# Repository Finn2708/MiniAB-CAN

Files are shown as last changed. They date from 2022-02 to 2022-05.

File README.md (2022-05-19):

# MiniAB-CAN
Toolhead board with CAN interface for [Voron Mini Afterburner](https://github.com/VoronDesign/Voron-0) and [Voron Stealthburner](https://github.com/VoronDesign/Voron-Afterburner/tree/sb-beta).

Features:
- CAN bus interface
- TMC2209 stepper driver for extruder motor
- Integrated ADXL345 for resonance compensation
- Neopixel Output for toolhead LEDs
- Two endstop and one probe port
- User-selectable fan voltages (5V/24V)

---

## Table of Contents
- [Prototype](#prototype)
  - [Size comparison](#size)
  - [Thermal images](#thermal-images)
- [Pinout](#pinout)
- [Interactive BOM](https://finn2708.github.io/MiniAB-CAN/index.html)

## Prototype
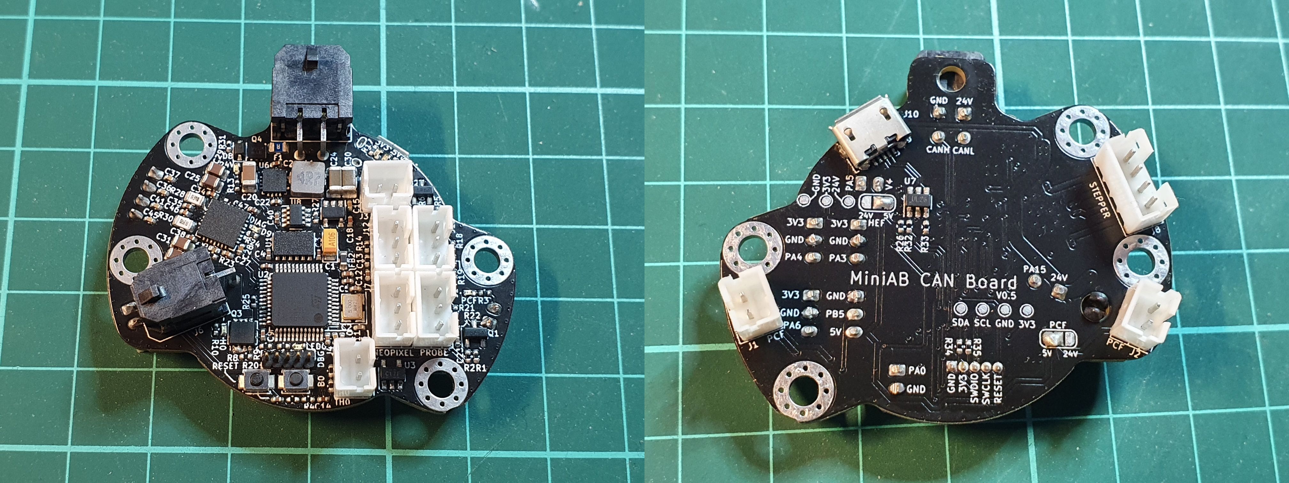
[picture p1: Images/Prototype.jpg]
Prototype


### Size
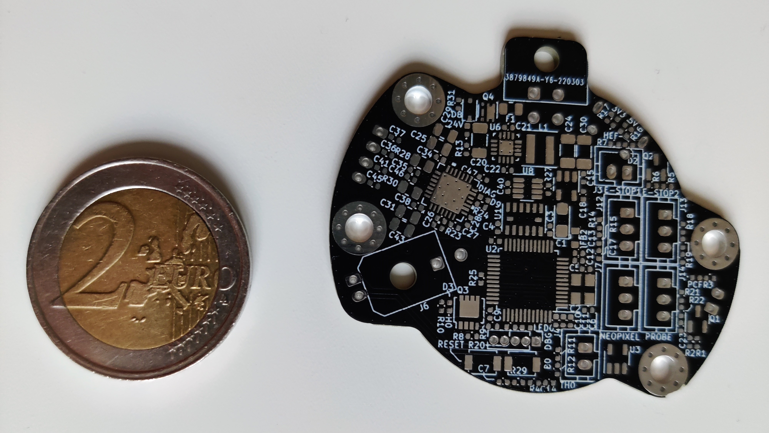
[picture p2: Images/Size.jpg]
Size


### Thermal images
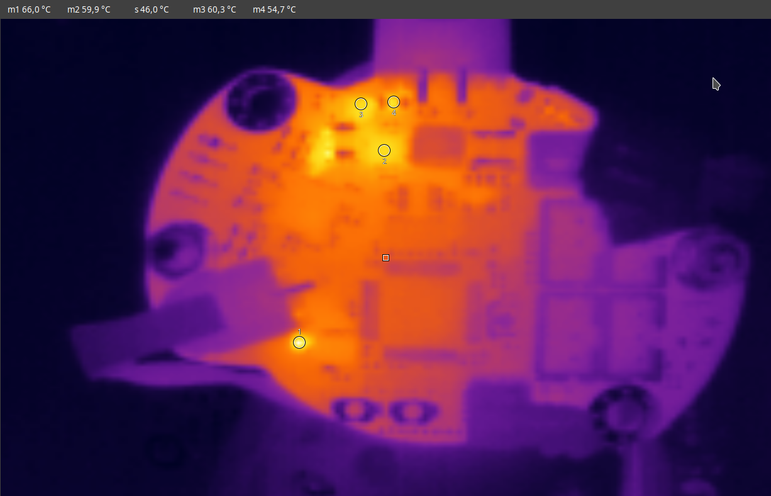
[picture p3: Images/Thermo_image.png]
Thermal images


## Pinout
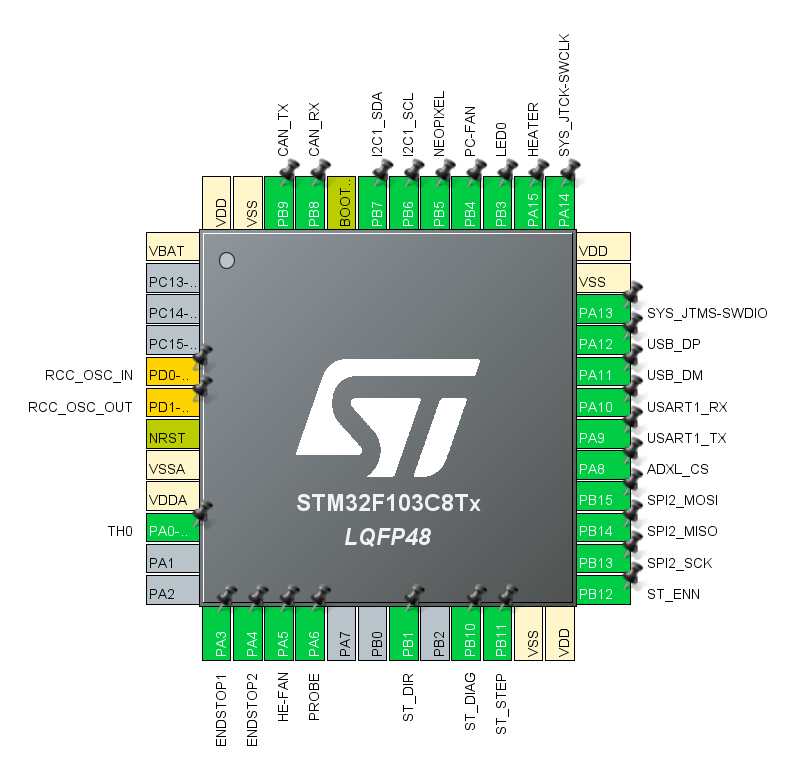
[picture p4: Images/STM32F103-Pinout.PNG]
Pinout

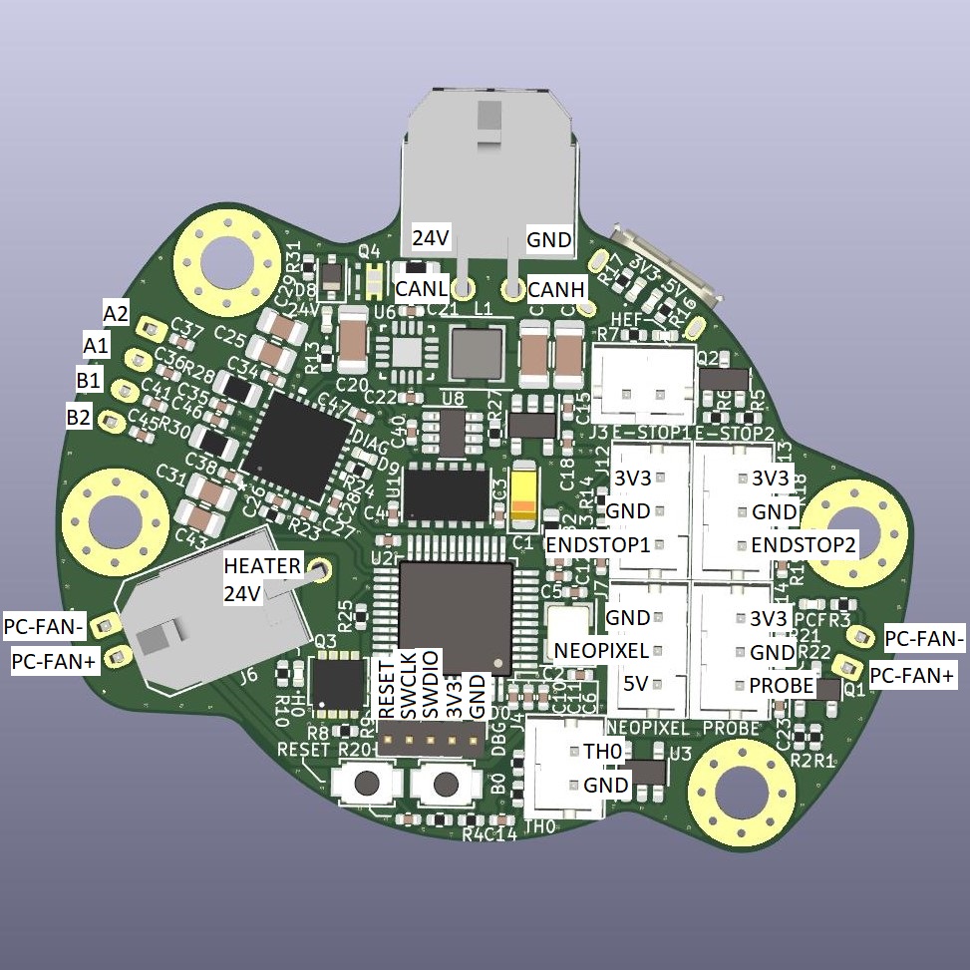
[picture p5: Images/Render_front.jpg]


## BOM
[Interactive BOM](https://finn2708.github.io/MiniAB-CAN/index.html)

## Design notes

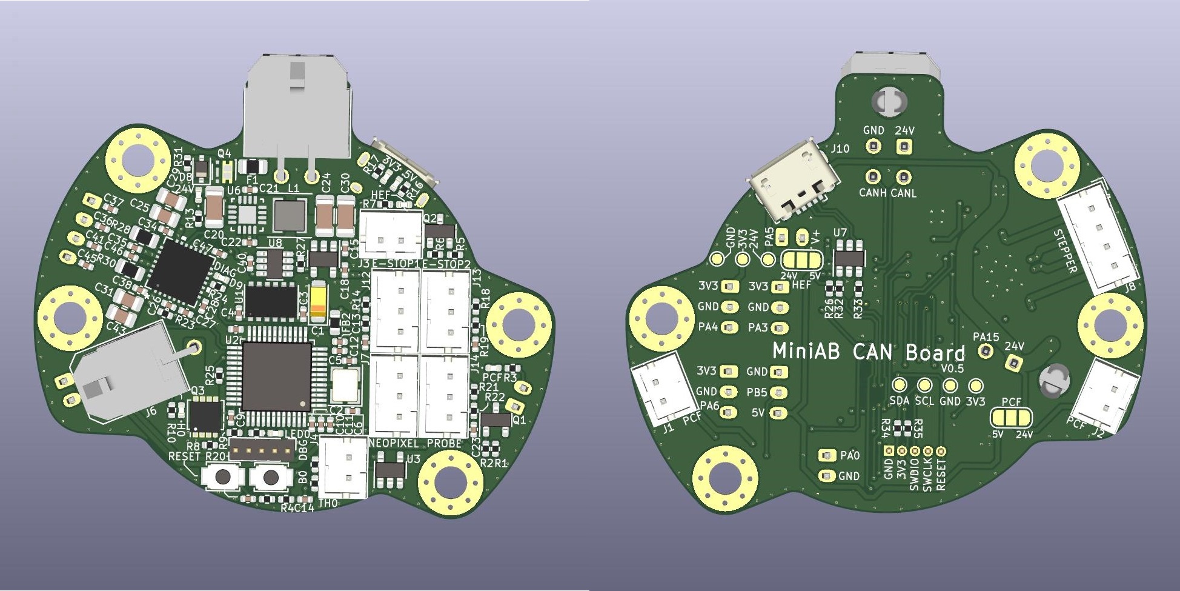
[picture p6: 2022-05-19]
Images/Render.jpg

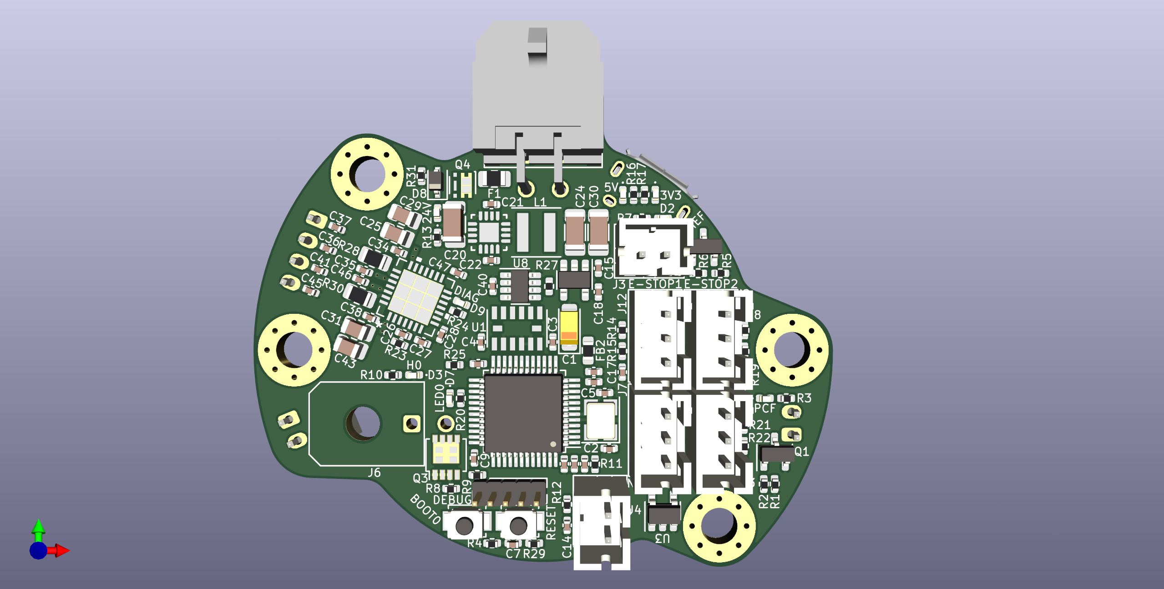
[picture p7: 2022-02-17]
PCB/MiniAB-CAN-Board_top.png

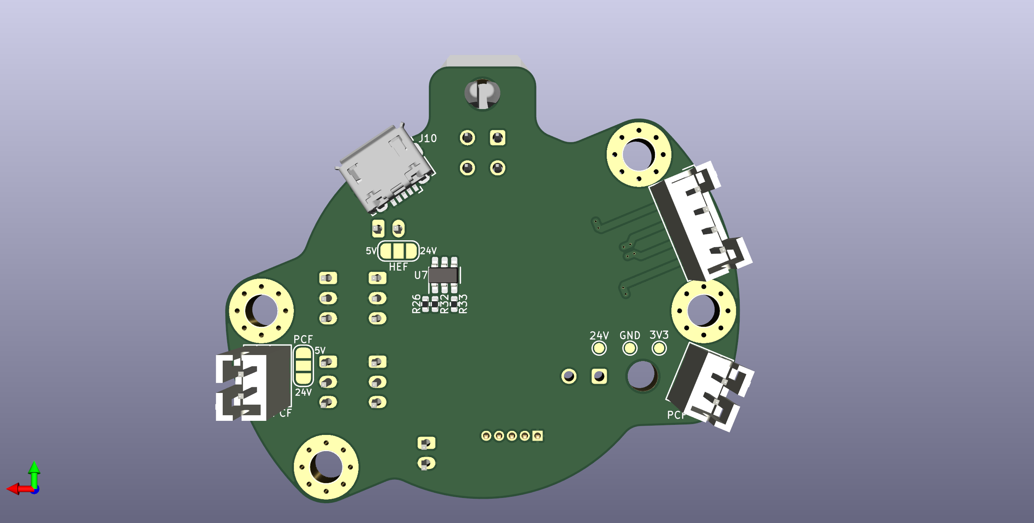
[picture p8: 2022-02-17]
PCB/MiniAB-CAN-Board_bottom.png

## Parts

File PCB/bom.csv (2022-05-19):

Comment | Designator | Footprint | LCSC
10u | C1 | Capacitor_Tantalum_SMD:CP_EIA-3216-18_Kemet-A
12p | C2,C5 | Capacitor_SMD:C_0402_1005Metric
100n | C3,C4,C6,C7,C8,C9,C10,C12,C14,C17,C19,C23,C40,C47 | Capacitor_SMD:C_0402_1005Metric
4.7u | C11,C28 | Capacitor_SMD:C_0402_1005Metric
1u | C13,C18 | Capacitor_SMD:C_0402_1005Metric
2u2 | C15 | Capacitor_SMD:C_0402_1005Metric
10u/35V | C20 | Capacitor_SMD:C_1206_3216Metric
100n/35V | C21,C27,C34,C35,C38,C46 | Capacitor_SMD:C_0402_1005Metric
22n | C22 | Capacitor_SMD:C_0402_1005Metric
22u | C24,C30 | Capacitor_SMD:C_1206_3216Metric
10u/35V | C25,C29,C31,C43 | Capacitor_SMD:C_0805_2012Metric
22n/50V | C26 | Capacitor_SMD:C_0402_1005Metric
1n/50V | C36,C37,C41,C45 | Capacitor_SMD:C_0402_1005Metric
RED | D1,D2,D3,D4,D5,D6,D7,D9 | LED_SMD:LED_0402_1005Metric
15V | D8 | Diode_SMD:D_SOD-323
3.5A | F1 | Fuse:Fuse_0805_2012Metric
GZ1608D601TF | FB2 | Resistor_SMD:R_0603_1608Metric
PCF | J1,J2 | Connector_JST:JST_PH_B2B-PH-K_1x02_P2.00mm_Vertical
HEF | J3 | Connector_JST:JST_PH_B2B-PH-K_1x02_P2.00mm_Vertical
TH0 | J4 | Connector_JST:JST_PH_B2B-PH-K_1x02_P2.00mm_Vertical
H0 | J6 | Connector_Molex:Molex_Micro-Fit_3.0_43045-0200_2x01_P3.00mm_Horizontal
NEOPIXEL | J7 | Connector_JST:JST_PH_B3B-PH-K_1x03_P2.00mm_Vertical
STEPPER | J8 | Connector_JST:JST_PH_B4B-PH-K_1x04_P2.00mm_Vertical
DEBUG | J9 | Connector_PinHeader_1.27mm:PinHeader_1x05_P1.27mm_Vertical
USB_B_Micro | J10 | Connector_USB:USB_Micro-B_Amphenol_10118194_Horizontal
CAN | J11 | Connector_Molex:Molex_Micro-Fit_3.0_43045-0400_2x02_P3.00mm_Horizontal
E-STOP1 | J12 | Connector_JST:JST_PH_B3B-PH-K_1x03_P2.00mm_Vertical
E-STOP2 | J13 | Connector_JST:JST_PH_B3B-PH-K_1x03_P2.00mm_Vertical
PROBE | J14 | Connector_JST:JST_PH_B3B-PH-K_1x03_P2.00mm_Vertical
4.7u | L1 | Inductor_SMD:L_Coilcraft_XxL4020
AO3400A | Q1,Q2 | Package_TO_SOT_SMD:SOT-23
AON7418 | Q3 | footprints:AON7418
SiA449DJ | Q4 | Package_TO_SOT_SMD:Vishay_PowerPAK_SC70-6L_Single
10k | R1,R4,R5,R8,R12,R14,R15,R18,R19,R21,R22 | Resistor_SMD:R_0402_1005Metric
150 | R2,R6,R9 | Resistor_SMD:R_0402_1005Metric
2.2k | R3,R7,R10,R13 | Resistor_SMD:R_0402_1005Metric
2.2k 0.1% | R11 | Resistor_SMD:R_0402_1005Metric
300 | R16 | Resistor_SMD:R_0402_1005Metric
120 | R17,R20,R24 | Resistor_SMD:R_0402_1005Metric
100k | R23,R29,R31 | Resistor_SMD:R_0402_1005Metric
1k | R25 | Resistor_SMD:R_0402_1005Metric
1.5k | R26 | Resistor_SMD:R_0402_1005Metric
120R | R27 | Resistor_SMD:R_0402_1005Metric
0.5Ω, 1%, 0.5W, 1210 | R28,R30 | Resistor_SMD:R_0805_2012Metric
27 | R32,R33 | Resistor_SMD:R_0402_1005Metric
4.7k | R34,R35 | Resistor_SMD:R_0402_1005Metric
RESET | SW1 | Button_Switch_SMD:SW_SPST_B3U-1000P
BOOT0 | SW2 | Button_Switch_SMD:SW_SPST_B3U-1000P
ADXL345BCCZ-RL7 | U1 | footprints:ADXL345BCCZ-RL7
STM32F103C8Tx | U2 | Package_QFP:LQFP-48_7x7mm_P0.5mm
74LVC1G17 | U3 | Package_TO_SOT_SMD:SOT-23-5
LP5907MFX-3.3 | U4 | Package_TO_SOT_SMD:SOT-23-5
TMC2209-LA | U5 | footprints:TMC2209-LA
TS30041-M050QFNR | U6 | TS30041:Semtech-QFN16-0-0-0
USBLC6-2SC6 | U7 | Package_TO_SOT_SMD:SOT-23-6
TCAN330 | U8 | Package_TO_SOT_SMD:TSOT-23-8
8MHz | Y1 | Crystal:Crystal_SMD_3225-4Pin_3.2x2.5mm

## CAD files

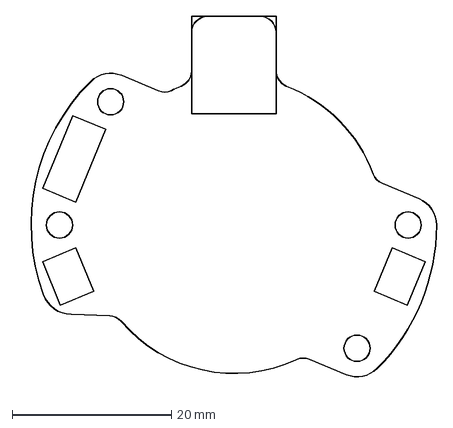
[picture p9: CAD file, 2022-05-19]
PCB/Outline.dxf
52.9 x 46.7 mm

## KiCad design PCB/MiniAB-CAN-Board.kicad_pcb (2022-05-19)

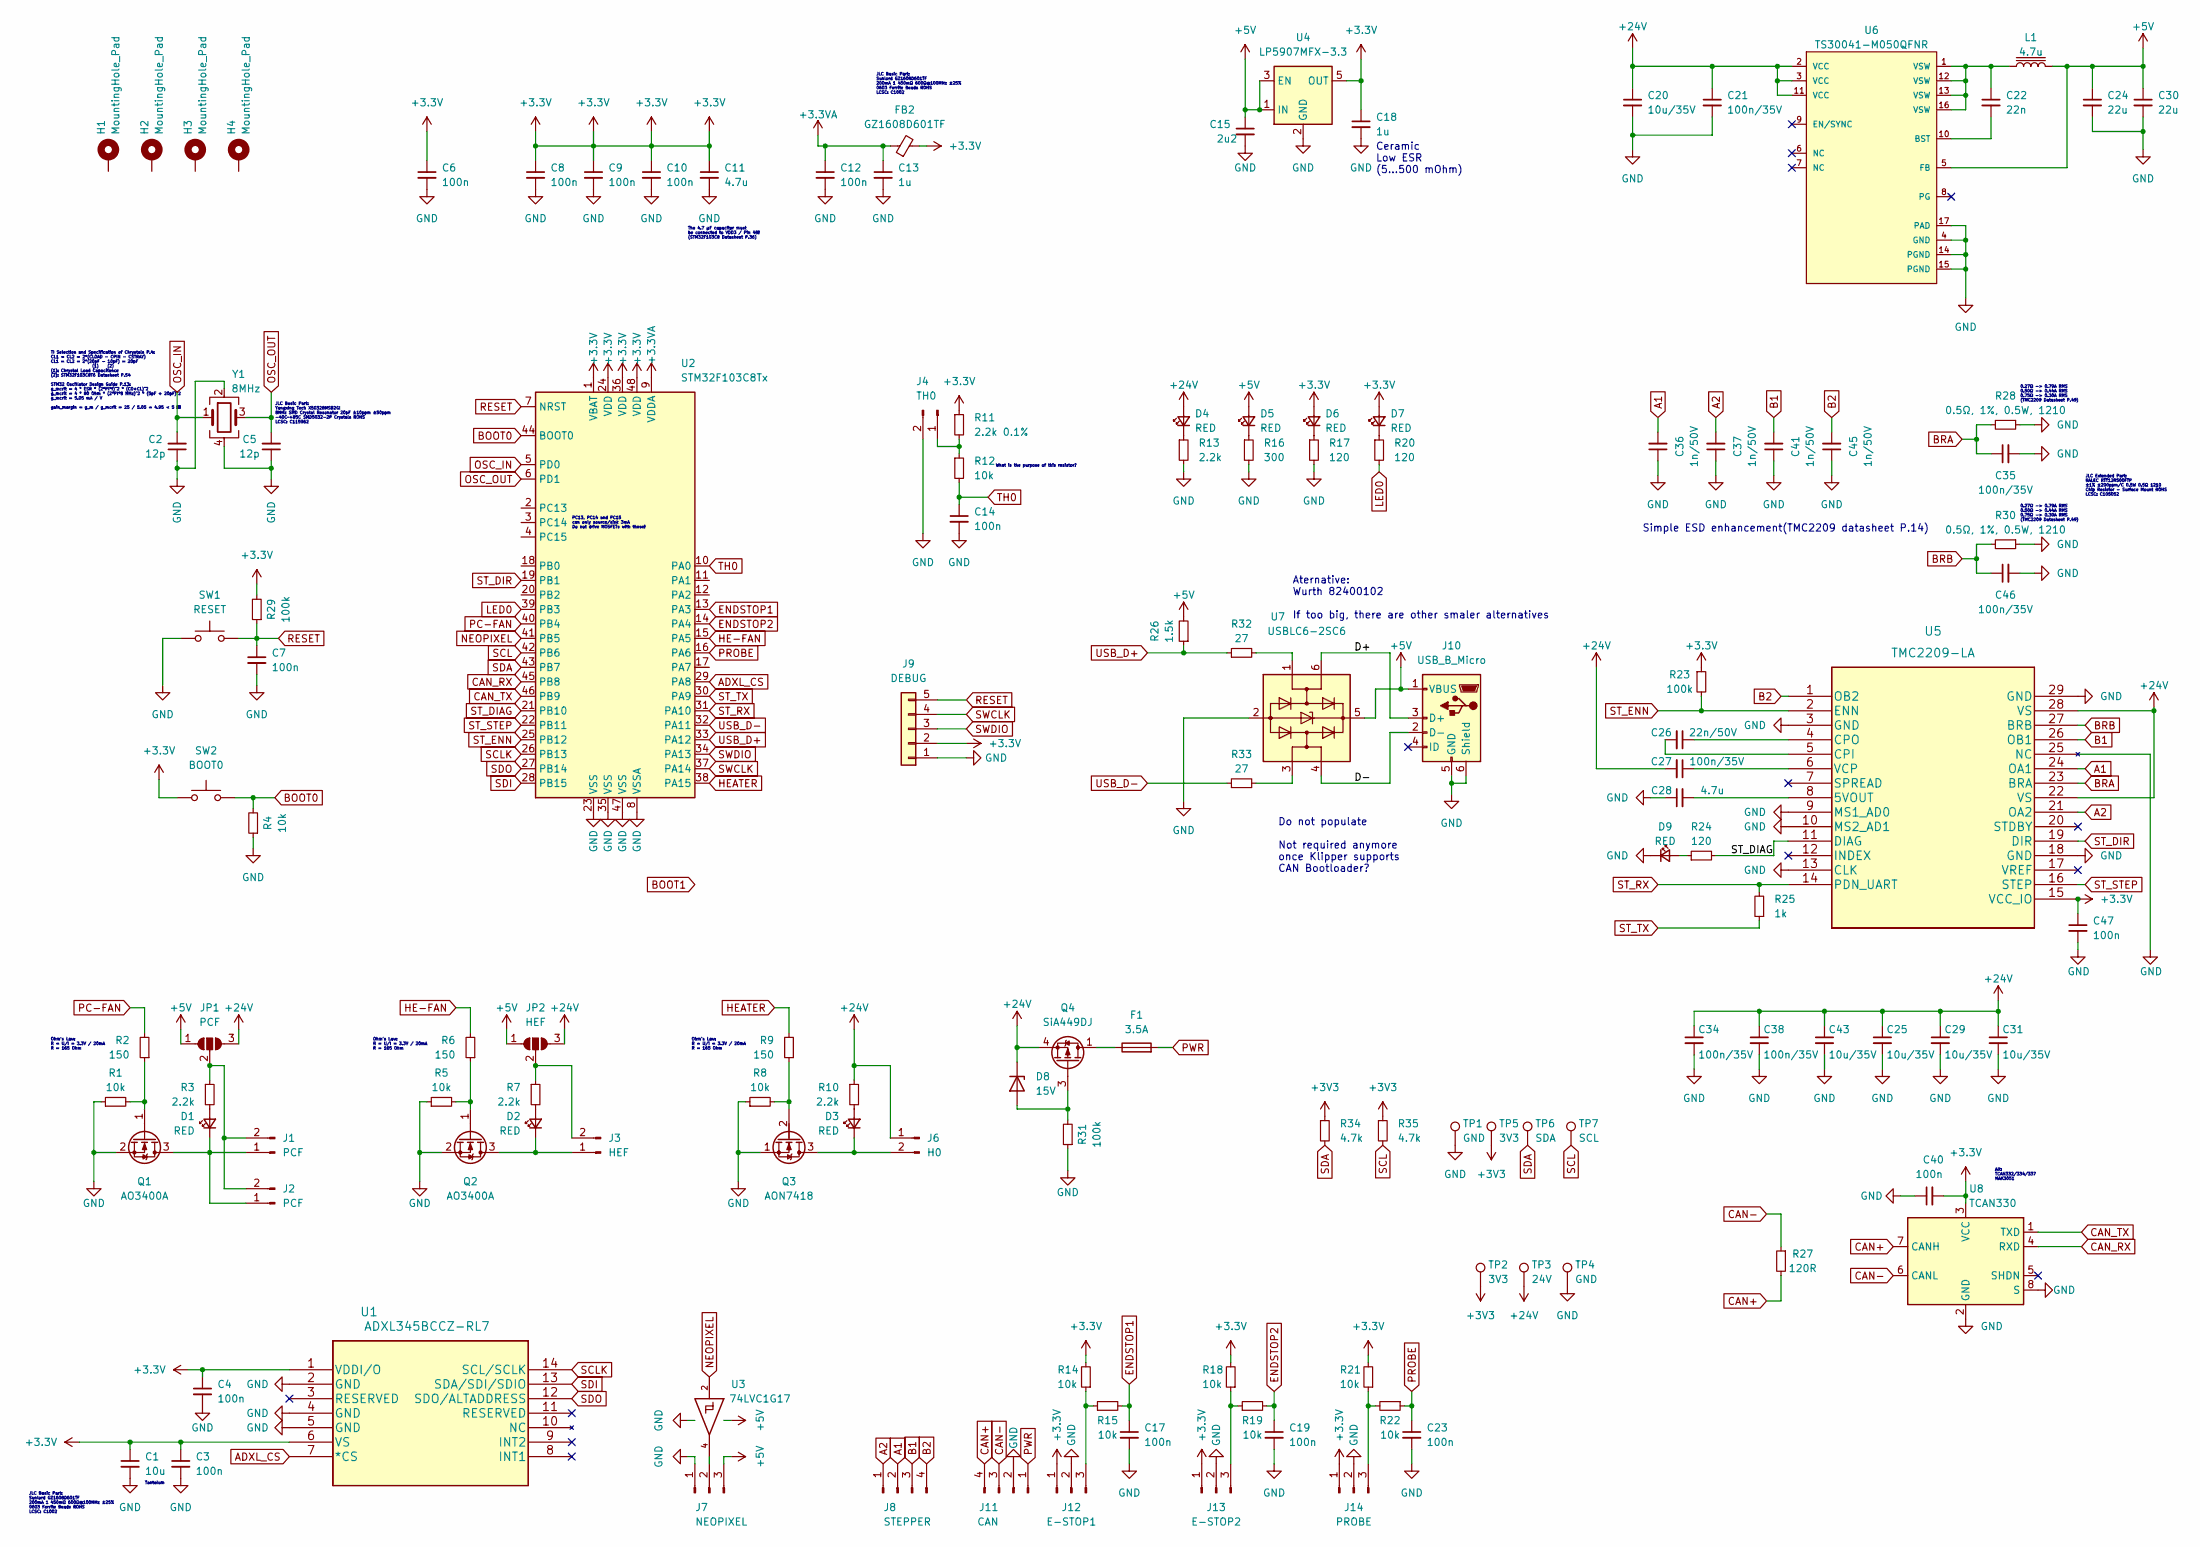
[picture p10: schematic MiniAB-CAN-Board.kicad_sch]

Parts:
C1: 10u; CP_EIA-3216-18_Kemet-A; MFG# TAJA106K016RNJ; LCSC# C7171
C2, C5: 12p; C_0402_1005Metric; MFG# C1005NP0120KGT; LCSC# C258502
C3, C4, C6, C7, C8, C9, C10, C12, C14, C17, C19, C23, C40, C47: 100n; C_0402_1005Metric; MFG# CL05B104KB54PNC; LCSC# C307331
C11, C28: 4.7u; C_0402_1005Metric; MFG# C0402X5R475M250NT; LCSC# C2911388
C13, C18: 1u; C_0402_1005Metric; MFG# CL05A105KA5NQNC; LCSC# C52923
C15: 2u2; C_0402_1005Metric; MFG# GRT155C71A225KE13D; LCSC# C415540
C20: 10u/35V; C_1206_3216Metric; MFG# GMK316AB7106KL-TR; LCSC# C454102
C21, C27, C34, C35, C38, C46: 100n/35V; C_0402_1005Metric; MFG# CL05B104KB54PNC; LCSC# C307331
C22: 22n; C_0402_1005Metric; MFG# CC0402KRX7R9BB223; LCSC# C107026
C24, C30: 22u; C_1206_3216Metric; MFG# C1206X7R226K160NT
C25, C29, C31, C43: 10u/35V; C_0805_2012Metric; MFG# C2012X5R1V226MT000E; LCSC# C338080
C26: 22n/50V; C_0402_1005Metric; MFG# 0402B223K500NT; LCSC# C1532
C36, C37, C41, C45: 1n/50V; C_0402_1005Metric; MFG# C0402C102K5RACAUTO; LCSC# C141053
D1, D2, D3, D4, D5, D6, D7, D9: RED; LED_0402_1005Metric
D8: 15V; D_SOD-323; MFG# SZMM3Z15VT1G; LCSC# C327522
F1: 3.5A; Fuse_0805_2012Metric; MFG# MFU0805FF03500P100; LCSC# C1972476
FB2: GZ1608D601TF; R_0603_1608Metric
H1, H2, H3, H4: MountingHole_Pad; MountingHole_3.2mm_M3_Pad_Via
J1, J2: PCF; JST_PH_B2B-PH-K_1x02_P2.00mm_Vertical
J3: HEF; JST_PH_B2B-PH-K_1x02_P2.00mm_Vertical
J4: TH0; JST_PH_B2B-PH-K_1x02_P2.00mm_Vertical
J6: H0; Molex_Micro-Fit_3.0_43045-0200_2x01_P3.00mm_Horizontal
J7: NEOPIXEL; JST_PH_B3B-PH-K_1x03_P2.00mm_Vertical
J8: STEPPER; JST_PH_B4B-PH-K_1x04_P2.00mm_Vertical
J9: DEBUG; PinHeader_1x05_P1.27mm_Vertical
J10: USB_B_Micro; USB_Micro-B_Amphenol_10118194_Horizontal
J11: CAN; Molex_Micro-Fit_3.0_43045-0400_2x02_P3.00mm_Horizontal
J12: E-STOP1; JST_PH_B3B-PH-K_1x03_P2.00mm_Vertical
J13: E-STOP2; JST_PH_B3B-PH-K_1x03_P2.00mm_Vertical
J14: PROBE; JST_PH_B3B-PH-K_1x03_P2.00mm_Vertical
JP1: PCF; SolderJumper-3_P1.3mm_Open_RoundedPad1.0x1.5mm_NumberLabels
JP2: HEF; SolderJumper-3_P1.3mm_Open_RoundedPad1.0x1.5mm_NumberLabels
L1: 4.7u; L_Coilcraft_XxL4020; MFG# MAPM0420F-4R7M-LF; LCSC# C280916
Q1, Q2: AO3400A; SOT-23
Q3: AON7418; MFG# AON7418; LCSC# C74384
Q4: SiA449DJ; Vishay_PowerPAK_SC70-6L_Single; MFG# SIA483DJ-T1-GE3; LCSC# C145467
R1, R4, R5, R8, R12, R14, R15, R18, R19, R21, R22: 10k; R_0402_1005Metric
R2, R6, R9: 150; R_0402_1005Metric
R3, R7, R10, R13: 2.2k; R_0402_1005Metric
R11: 2.2k 0.1%; R_0402_1005Metric
R16: 300; R_0402_1005Metric
R17, R20, R24: 120; R_0402_1005Metric
R23, R29, R31: 100k; R_0402_1005Metric
R25: 1k; R_0402_1005Metric
R26: 1.5k; R_0402_1005Metric; MFG# 0402WGJ0152TCE; LCSC# C25930
R27: 120R; R_0402_1005Metric; MFG# 0402WGF1200TCE; LCSC# C25079
R28, R30: 0.5Ω, 1%, 0.5W, 1210; R_0805_2012Metric
R32, R33: 27; R_0402_1005Metric; MFG# ERJ2RKF27R0X; LCSC# C413051
R34, R35: 4.7k; R_0402_1005Metric
SW1: RESET; SW_SPST_B3U-1000P; MFG# B3U-1000P; LCSC# C231329
SW2: BOOT0; SW_SPST_B3U-1000P; MFG# B3U-1000P; LCSC# C231329
TP1, TP4: GND; TestPoint_Pad_D1.0mm
TP2, TP5: 3V3; TestPoint_Pad_D1.0mm
TP3: 24V; TestPoint_Pad_D1.0mm
TP6: SDA; TestPoint_Pad_D1.0mm
TP7: SCL; TestPoint_Pad_D1.0mm
U1: ADXL345BCCZ-RL7
U2: STM32F103C8Tx; LQFP-48_7x7mm_P0.5mm
U3: 74LVC1G17; SOT-23-5
U4: LP5907MFX-3.3; SOT-23-5
U5: TMC2209-LA
U6: TS30041-M050QFNR; Semtech-QFN16-0-0-0; output voltage 5V; mouser part number 947-TS30041-M050QFNR; digikey description IC REG BUCK 5V 1A SYNC 16-VQFN
U7: USBLC6-2SC6; SOT-23-6; MFG# USBLC6-2SC6; LCSC# C7519
U8: TCAN330; TSOT-23-8
Y1: 8MHz; Crystal_SMD_3225-4Pin_3.2x2.5mm; MFG# TAXM8M4RFDCET2T; LCSC# C403948

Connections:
+3.3VA: C12.1, C13.1, FB2.1, U2.9 (VDDA)
+5V: C15.1, C24.1, C30.1, D5.2 (A), J7.3, J10.1 (VBUS), JP1.1 (A), JP2.1 (A), L1.2, R26.2, U3.5 (VCC), U4.1 (IN), U4.3 (EN), U6.5 (FB), U7.5 (VBUS)
+24V: C20.1, C21.1, C25.1, C27.2, C29.1, C31.1, C34.1, C38.1, C43.1, D4.2 (A), D8.1 (K), J6.1, JP1.3 (B), JP2.3 (B), Q4.4 (S), R10.1, TP3.1, U5.22 (VS), U5.28 (VS), U6.2 (VCC), U6.3 (VCC), U6.11 (VCC)
/D+: J10.3 (D+), U7.6 (I/O1)
/D-: J10.2 (D-), U7.4 (I/O2)
A1: C36.2, J8.2, U5.24 (OA1)
A2: C37.2, J8.1, U5.21 (OA2)
ADXL_CS: U1.7 (*CS), U2.29 (PA8)
B1: C41.2, J8.3, U5.26 (OB1)
B2: C45.2, J8.4, U5.1 (OB2)
BOOT0: R4.2, SW2.2, U2.44 (BOOT0)
BRA: C35.1, R28.2, U5.23 (BRA)
BRB: C46.1, R30.2, U5.27 (BRB)
CAN+: J11.4, R27.2, U8.7 (CANH)
CAN-: J11.3, R27.1, U8.6 (CANL)
CAN_RX: U2.45 (PB8), U8.4 (RXD)
CAN_TX: U2.46 (PB9), U8.1 (TXD)
ENDSTOP1: C17.1, R15.2, U2.13 (PA3)
ENDSTOP2: C19.1, R19.2, U2.14 (PA4)
GND: C1.2, C2.1, C3.2, C4.2, C5.1, C6.2, C7.2, C8.2, C9.2, C10.2, C11.2, C12.2, C13.2, C14.2, C15.2, C17.2, C18.2, C19.2, C20.2, C21.2, C23.2, C24.2, C25.2, C28.1, C29.2, C30.2, C31.2, C34.2, C35.2, C36.1, C37.1, C38.2, C40.1, C41.1, C43.2, C45.1, C46.2, C47.2, D9.1 (K), J4.2, J7.1, J9.1, J10.5 (GND), J10.6 (Shield), J11.2, J12.2, J13.2, J14.2, Q1.2 (S), Q2.2 (S), Q3.1 (S), R1.1, R4.1, R5.1, R8.1, R13.2, R16.2, R17.2, R28.1, R30.1, R31.1, SW1.1, TP1.1, TP4.1, U1.2 (GND), U1.4 (GND), U1.5 (GND), U2.8 (VSSA), U2.23 (VSS), U2.35 (VSS), U2.47 (VSS), U3.3 (GND), U4.2 (GND), U5.3 (GND), U5.9 (MS1_AD0), U5.10 (MS2_AD1), U5.13 (CLK), U5.18 (GND), U5.25 (NC), U5.29 (GND), U6.4 (GND), U6.14 (PGND), U6.15 (PGND), U6.17 (PAD), U7.2 (GND), U8.2 (GND), U8.8 (S), Y1.2, Y1.4
HE-FAN: R6.2, U2.15 (PA5)
HEATER: R9.2, U2.38 (PA15)
LED0: R20.2, U2.39 (PB3)
NEOPIXEL: U2.41 (PB5), U3.2
unnamed: C22.1, L1.1, U6.1 (VSW), U6.12 (VSW), U6.13 (VSW), U6.16 (VSW)
unnamed: C22.2, U6.10 (BST)
unnamed: C26.1, U5.4 (CPO)
unnamed: C26.2, U5.5 (CPI)
unnamed: C27.1, U5.6 (VCP)
unnamed: C28.2, U5.8 (5VOUT)
unnamed: D1.1 (K), J1.1, J2.1, Q1.3 (D)
unnamed: D1.2 (A), R3.2
unnamed: D2.1 (K), J3.1, Q2.3 (D)
unnamed: D2.2 (A), R7.2
unnamed: D3.1 (K), J6.2, Q3.3 (D)
unnamed: D3.2 (A), R10.2
unnamed: D4.1 (K), R13.1
unnamed: D5.1 (K), R16.1
unnamed: D6.1 (K), R17.1
unnamed: D7.1 (K), R20.1
unnamed: D8.2 (A), Q4.3 (G), R31.2
unnamed: D9.2 (A), R24.1
unnamed: F1.1, Q4.1 (D)
unnamed: J1.2, J2.2, JP1.2 (C), R3.1
unnamed: J3.2, JP2.2 (C), R7.1
unnamed: J4.1, R11.2, R12.1
unnamed: J7.2, U3.4
unnamed: J12.3, R14.1, R15.1
unnamed: J13.3, R18.1, R19.1
unnamed: J14.3, R21.1, R22.2
unnamed: Q1.1 (G), R1.2, R2.1
unnamed: Q2.1 (G), R5.2, R6.1
unnamed: Q3.2 (G), R8.2, R9.1
unnamed: R32.2, U7.1 (I/O1)
unnamed: R33.2, U7.3 (I/O2)
OSC_IN: C2.2, U2.5 (PD0), Y1.1
OSC_OUT: C5.2, U2.6 (PD1), Y1.3
PC-FAN: R2.2, U2.40 (PB4)
PROBE: C23.1, R22.1, U2.16 (PA6)
PWR: F1.2, J11.1
RESET: C7.1, J9.5, R29.1, SW1.2, U2.7 (NRST)
SCL: R35.2, TP7.1, U2.42 (PB6)
SCLK: U1.14 (SCL/SCLK), U2.26 (PB13)
SDA: R34.2, TP6.1, U2.43 (PB7)
SDI: U1.13 (SDA/SDI/SDIO), U2.28 (PB15)
SDO: U1.12 (SDO/ALTADDRESS), U2.27 (PB14)
ST_DIAG: R24.2, U2.21 (PB10), U5.11 (DIAG)
ST_DIR: U2.19 (PB1), U5.19 (DIR)
ST_ENN: R23.2, U2.25 (PB12), U5.2 (ENN)
ST_RX: R25.2, U2.31 (PA10), U5.14 (PDN_UART)
ST_STEP: U2.22 (PB11), U5.16 (STEP)
ST_TX: R25.1, U2.30 (PA9)
SWCLK: J9.4, U2.37 (PA14)
SWDIO: J9.3, U2.34 (PA13)
TH0: C14.1, R12.2, U2.10 (PA0)
USB_D+: R26.1, R32.1, U2.33 (PA12)
USB_D-: R33.1, U2.32 (PA11)

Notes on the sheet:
Ohm's Law: R = U/I = 3.3V / 20mA R = 165 Ohm
Do not populate Not required anymore once Klipper supports CAN Bootloader?
What is the purpose of this resistor?
0.27Ω -> 0.79A RMS 0.50Ω -> 0.44A RMS 0.75Ω -> 0.30A RMS (TMC2209 Datasheet P.49)
The 4.7 µF capacitor must be connected to VDD3 / Pin 48! (STM32F103C8 Datasheet P.36)
Alt: TCAN332/334/337 MAX3051
Tantalum
Aternative: Wurth 82400102 If too big, there are other smaler alternatives
JLC Basic Part: Sunlord GZ1608D601TF 200mA 1 450mΩ 600Ω@100MHz ±25% 0603 Ferrite Beads ROHS LCSC: C1002
PC13, PC14 and PC15 can only source/sink 3mA Do not drive MOSFETs with these!
Ceramic Low ESR (5...500 mOhm)
JLC Extended Part: RALEC RTT12R500FTP ±1% ±200ppm/C 0.5W 0.5Ω 1210 Chip Resistor - Surface Mount ROHS LCSC: C105052
TI Selection and Specification of Chrystals P.4: CL1 = CL2 = 2*(CLOAD - CPIN - CSTRAY) CL1 = CL2 = 2*(20pF - 10pF) = 20pF (1) (2) (1): Chrystal Load Capacitance (2): STM32F103C8T6 Datasheet P.54 STM32 Oscillator Design Guide P.13: g_mcrit = 4 * ESR * (2*PI*f)^2 * (C0+CL)^2 g_mcrit = 4 * 80 Ohm * (2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
JLC Basic Part: Yangxing Tech X50328MSB2GI 8MHz SMD Crystal Resonator 20pF ±10ppm ±50ppm -40C~+85C SMD5032-2P Crystals ROHS LCSC: C115962
Simple ESD enhancement(TMC2209 datasheet P.14)

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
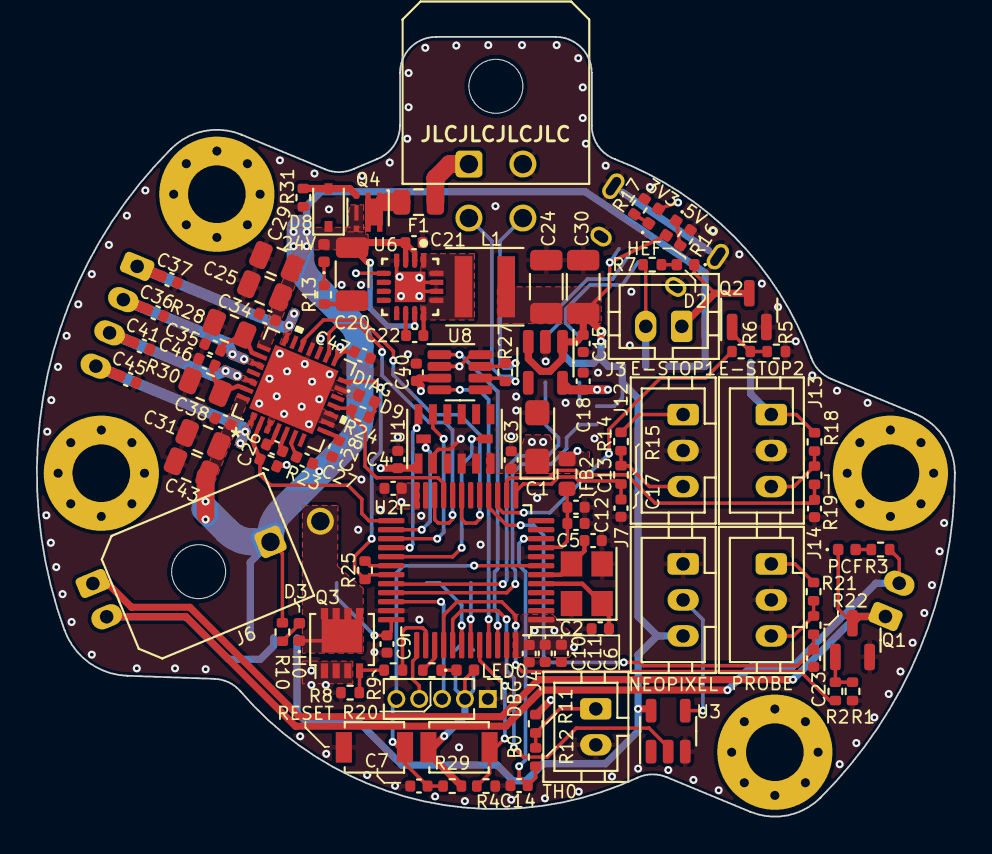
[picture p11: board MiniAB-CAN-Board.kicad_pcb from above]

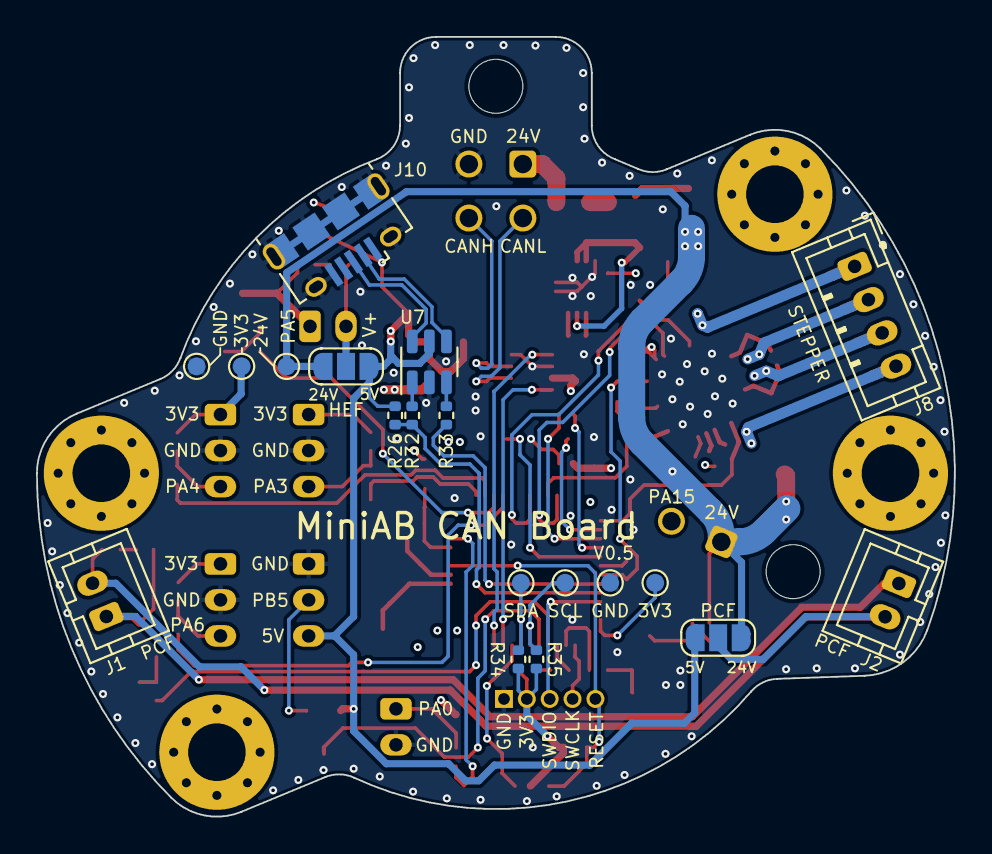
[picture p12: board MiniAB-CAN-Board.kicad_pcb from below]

Board: 4 copper layers, 51.0 x 43.3 mm, 129 parts (19 on the bottom side), 78 nets.

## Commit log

2021-11-29 Fix library imports
    [MiniAB-CAN-Board.kicad_pcb, MiniAB-CAN-Board.sch]
2021-12-02 Add exposed copper pad for heat sink
    [MiniAB-CAN-Board.kicad_pcb]
2021-12-02 Heatsink oriented at 45deg because 24V conflict
    [MiniAB-CAN-Board.kicad_pcb]
2021-12-12 Add BOM
    [MiniAB-CAN-Board.xlsx]
2021-12-12 Updates to PCB
    [MiniAB-CAN-Board-B_Cu.gbr, MiniAB-CAN-Board-B_Mask.gbr, MiniAB-CAN-Board-B_Paste.gbr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]
2021-12-14 add debug port and rework of schematic
    [MiniAB-CAN-Board.sch]
2021-12-14 Add 3 Pin Endstops + LED Port
    [MiniAB-CAN-Board.sch]
2021-12-15 change rgb led pin order, some rearrangements
    [MiniAB-CAN-Board.sch]
2021-12-20 add missing footprints
    [MiniAB-CAN-Board.sch]
2021-12-26 Add preliminary V0.2
    [MiniAB-CAN-Board-B_Cu.gbr, MiniAB-CAN-Board-B_Mask.gbr, MiniAB-CAN-Board-B_Paste.gbr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]
2021-12-30 complete routing, repair zones, review back side
    [MiniAB-CAN-Board.kicad_sch]
2021-12-31 Add TMC2209 to V0.3 Schematic
    [MiniAB-CAN-Board.kicad_pcb, MiniAB-CAN-Board.kicad_sch]
2021-12-31 Add STM32 and ADXL to V0.3 Schematic
    [MiniAB-CAN-Board.kicad_sch]
2022-01-02 Update V0.3 schematic
    [MiniAB-CAN-Board.kicad_pcb, MiniAB-CAN-Board.kicad_sch]
2022-01-02 Update footprints for V0.3
    [MiniAB-CAN-Board.kicad_sch]
2022-01-02 Chrystal Design done
    [MiniAB-CAN-Board.kicad_pcb, MiniAB-CAN-Board.kicad_sch]
2022-01-03 PCB Layout V0.3 WIP
    [MiniAB-CAN-Board.kicad_pcb, MiniAB-CAN-Board.kicad_sch]
2022-01-03 Updated footprints to 0402 if possible
    [MiniAB-CAN-Board.kicad_pcb, MiniAB-CAN-Board.kicad_sch]
2022-01-04 TMC added to V0.3
    [MiniAB-CAN-Board.kicad_pcb, MiniAB-CAN-Board.kicad_sch]
2022-01-04 Finished Front Side
    [MiniAB-CAN-Board.kicad_pcb, MiniAB-CAN-Board.kicad_sch]
2022-01-04 Fix merge issues
    [MiniAB-CAN-Board.kicad_pcb, MiniAB-CAN-Board.kicad_sch]
2022-01-04 Update Fan Mosfet Placement
    [MiniAB-CAN-Board.kicad_pcb]
2022-01-04 Stuck on connector placement
    [MiniAB-CAN-Board.kicad_pcb, MiniAB-CAN-Board.kicad_sch]
2022-01-05 Start new experimental design
    [MiniAB-CAN-Board.kicad_pcb, MiniAB-CAN-Board.kicad_sch]
2022-01-06 Add THT JST version with new DCDC converter
    [MiniAB-CAN-Board.kicad_pcb, MiniAB-CAN-Board.kicad_sch]
2022-01-06 Update PCB
    [MiniAB-CAN-Board.kicad_pcb]
2022-01-06 Update DCDC Section
    [MiniAB-CAN-Board.kicad_pcb, MiniAB-CAN-Board.kicad_sch]
2022-01-08 V0.4 finished
    [MiniAB-CAN-Board.kicad_pcb, MiniAB-CAN-Board.kicad_sch]
2022-01-08 Fix GND connection on TCAN330
    [MiniAB-CAN-Board.kicad_pcb, MiniAB-CAN-Board.kicad_sch]
2022-01-08 Add silkscreen annotations
    [MiniAB-CAN-Board.kicad_pcb, MiniAB-CAN-Board.kicad_sch]
2022-01-08 Add step models for CAD export
    [MiniAB-CAN-Board.kicad_pcb]
2022-01-08 Update Step model
    [MiniAB-CAN-Board.kicad_pcb]
2022-01-09 Add gerbers
    [MiniAB-CAN-Board-CmtUser.gbr, MiniAB-CAN-Board-CuBottom.gbl, MiniAB-CAN-Board-CuTop.gtl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]
2022-01-14 Fix minor issues on schematic, pcb still pending
    [MiniAB-CAN-Board.kicad_sch]
2022-02-04 add polarity check, change crystal, change debug, add buttons, exchange 5V regulator, correct MOSFETs, updated TMC2209 and all capacitors
    [MiniAB-CAN-Board.kicad_pcb, MiniAB-CAN-Board.kicad_sch]
2022-02-06 reduces CAN interface, complets USB interface, add new mounting holes
    [MiniAB-CAN-Board.kicad_pcb, MiniAB-CAN-Board.kicad_sch]
2022-02-13 Add single sided version
    [MiniAB-CAN-Board-CmtUser.gbr, MiniAB-CAN-Board-CuBottom.gbl, MiniAB-CAN-Board-CuTop.gtl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]
2022-02-17 JNP Layout and first routings
    [MiniAB-CAN-Board.kicad_pcb, MiniAB-CAN-Board.kicad_sch]
2022-02-17 Routing finished
    [MiniAB-CAN-Board.kicad_pcb, MiniAB-CAN-Board.kicad_sch]
2022-02-17 Add vias to board edge
    [MiniAB-CAN-Board.kicad_pcb]
2022-02-17 Update routing
    [MiniAB-CAN-Board.kicad_pcb, MiniAB-CAN-Board.kicad_sch]
2022-02-22 Update silk screen
    [MiniAB-CAN-Board.kicad_pcb]
2022-02-24 Update silkscreen
    [MiniAB-CAN-Board.kicad_pcb]
2022-02-27 Update BOM
    [MiniAB-CAN-Board.csv, MiniAB-CAN-Board.kicad_pcb, MiniAB-CAN-Board.kicad_sch]
2022-05-19 Add pinout
    [BOM.xlsx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]
2022-05-19 Add interactive BOM

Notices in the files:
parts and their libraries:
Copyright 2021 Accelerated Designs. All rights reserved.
